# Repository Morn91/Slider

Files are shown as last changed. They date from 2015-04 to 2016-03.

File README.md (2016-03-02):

## Слайдер


#### Особенности устройства
- Вес всего 2 килограмма.
- Единственная центральная точка опоры.
- Возможность работы вертикально, перевернуто и т.д.
- Предназначение для компактных камер и гибридов (за которыми будущее).
- [Управление со смартфона по Bluetooth](https://github.com/Morn91/Slider_Android_App).
- Небольшая цена порядка $100.

#### Важно!
Проект (устройство / изделие / агрегат) еще весьма сырой, требует много доработок (особенно [приложение для Android](https://github.com/Morn91/Slider_Android_App)), однако уже вполне работает.

Имейте ввиду, я делал его как очень легкий, под очень легкую камеру (Nikon Coolpix A, весом 300 грамм). Слайдер может не поднять тяжелую БЧЗ при вертикальной работе или опрокидываться / крениться с ней при работе горизонтальной. Лучше всего использовать его с камерами вроде моей, Sony NEX, GoPro и т.д.

Мне бы не помешала помощь в развитии устройства. Если возьметесь делать его — не забывайте делиться результатами, трудностями и вносимыми изменениями.

#### [Инструкция (ru)](https://github.com/Morn91/Slider/issues/1)

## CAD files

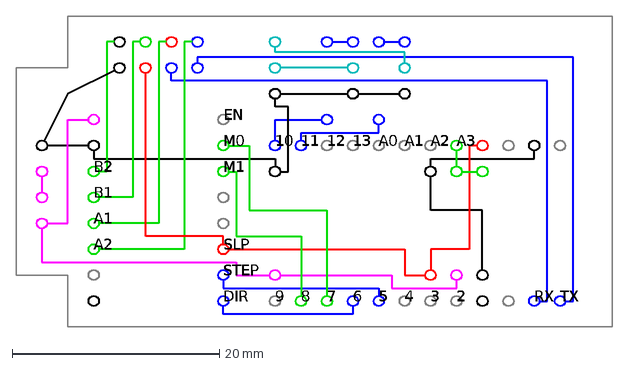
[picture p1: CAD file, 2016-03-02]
Drawings/Scheme.dxf
9
8
7
6
5
4
3
2
RX
TX
10
11
12
13
A0
A1
A2
A3
B2
B1
EN
M0
M1
SLP
STEP
DIR

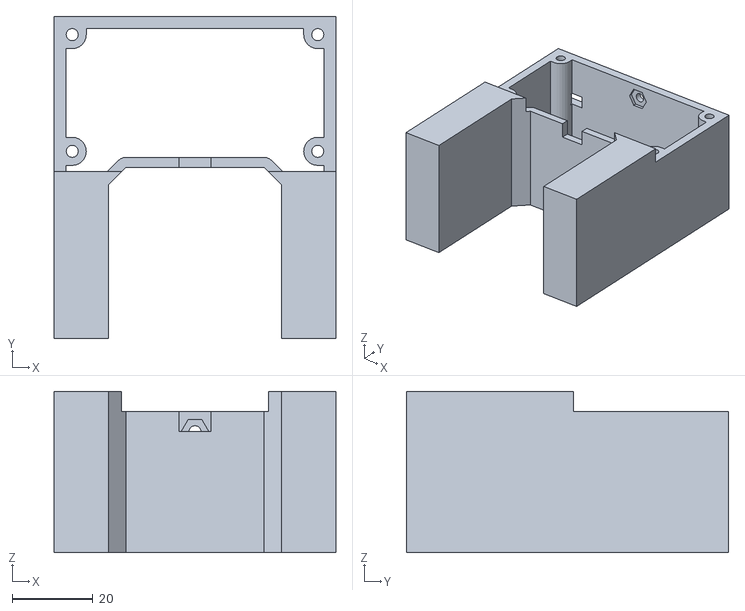
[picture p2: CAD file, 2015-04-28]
Drawings/Enclosure.stl
70.0 x 80.0 x 40.0

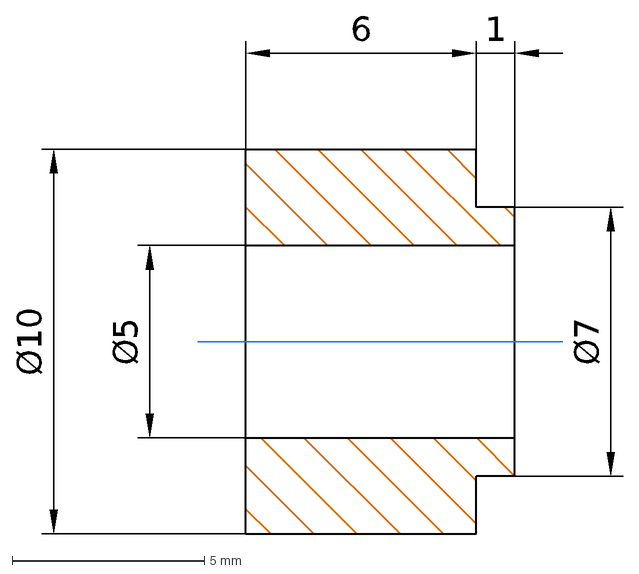
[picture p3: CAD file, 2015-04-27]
Drawings/Spacer.dxf
Ø10
Ø5
Ø7
6
1

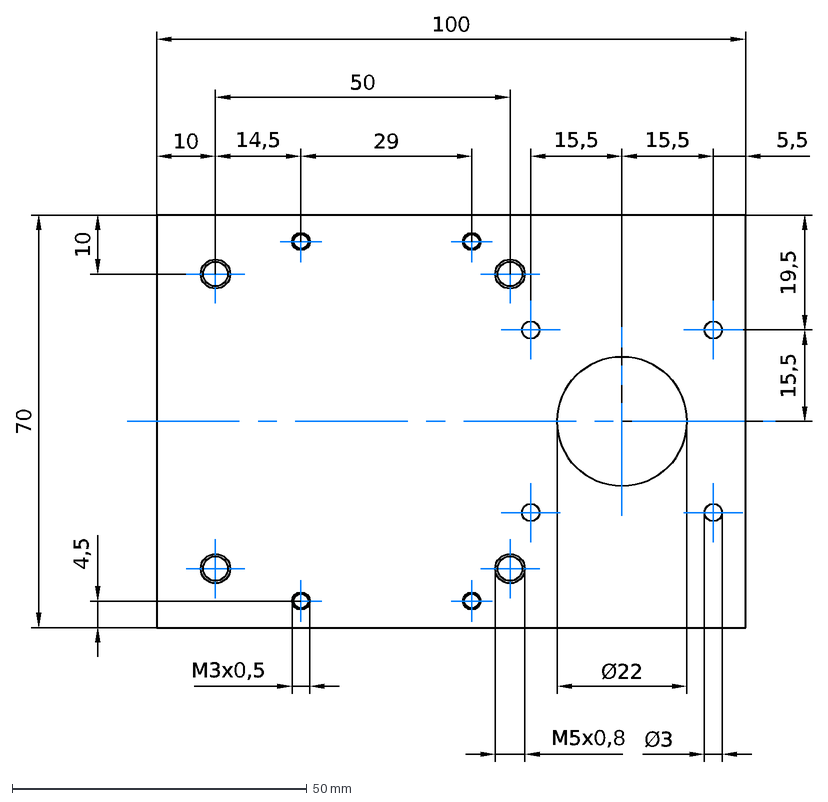
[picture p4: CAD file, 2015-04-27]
Drawings/Plate.dxf
70
14,5
100
10
М5x0,8
Ø3
15,5
5,5
19,5
Ø22
М3х0,5
29
4,5
50

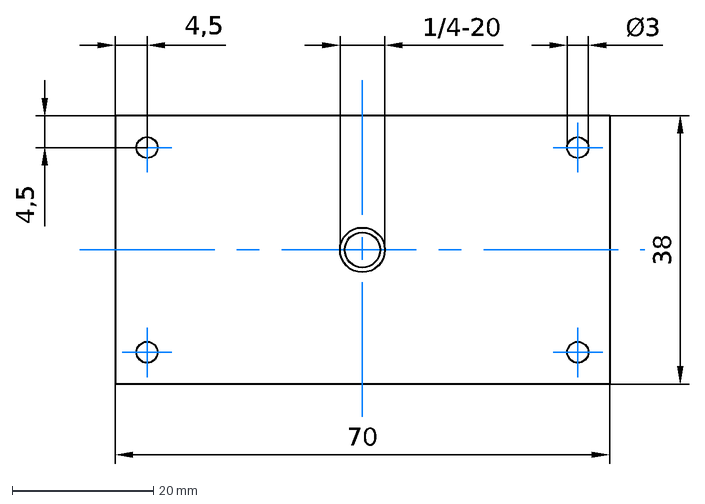
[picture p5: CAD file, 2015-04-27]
Drawings/Cover.dxf
Ø3
38
70
1/4-20
4,5

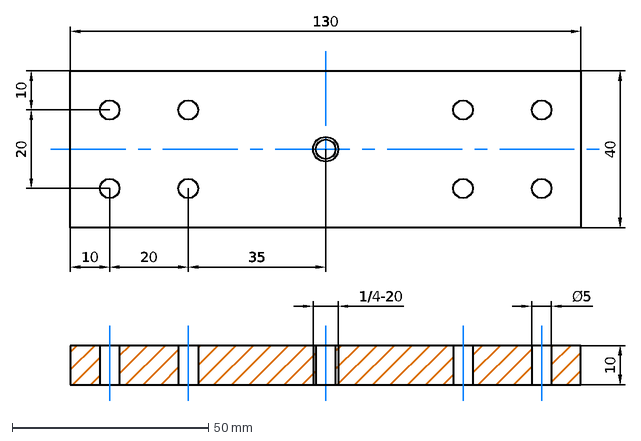
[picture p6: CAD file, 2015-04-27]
Drawings/Holder.dxf
Ø5
20
130
10
1/4-20
40
35

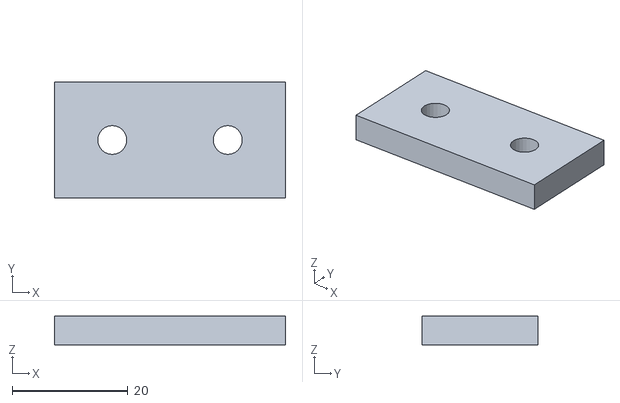
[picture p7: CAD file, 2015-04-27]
Drawings/Stopper.stl
40.0 x 20.0 x 5.00

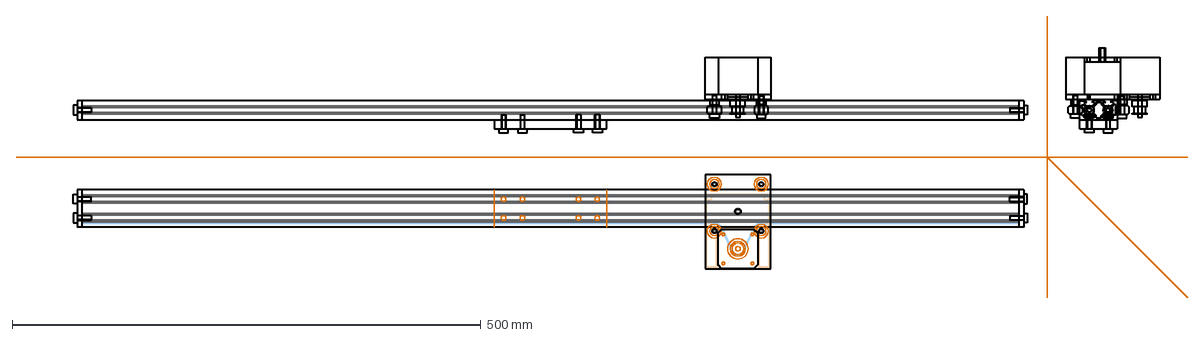
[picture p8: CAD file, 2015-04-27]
Drawings/General_view.dxf
1250.0 x 300.0 mm

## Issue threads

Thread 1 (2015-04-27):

Сборка (ru)

Morn91, 2015-04-27:
## Самодельные детали
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
#### Делаются на фрезеровочном станке:
##### Площадка ([Plate.dxf](https://github.com/Morn91/Slider/blob/master/Drawings/Plate.dxf))
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
##### Крышка ([Cover.dxf](https://github.com/Morn91/Slider/blob/master/Drawings/Cover.dxf))
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
##### Держатель ([Holder.dxf](https://github.com/Morn91/Slider/blob/master/Drawings/Holder.dxf))
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
#### Делаются на токарном станке:
##### Втулки ([Spacer.dxf](https://github.com/Morn91/Slider/blob/master/Drawings/Spacer.dxf))
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
#### Печатаются на 3D-принтере:
##### Корпус ([Enclosure.stl](https://github.com/Morn91/Slider/blob/master/Drawings/Enclosure.stl))
##### Стопоры ([Stopper.stl](https://github.com/Morn91/Slider/blob/master/Drawings/Stopper.stl))

Morn91, 2015-04-27:
## Самодельные детали
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
#### Делаются на фрезеровочном станке:
##### Площадка ([Plate.dxf](https://github.com/Morn91/Slider/blob/master/Drawings/Plate.dxf))
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
##### Крышка ([Cover.dxf](https://github.com/Morn91/Slider/blob/master/Drawings/Cover.dxf))
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
##### Держатель ([Holder.dxf](https://github.com/Morn91/Slider/blob/master/Drawings/Holder.dxf))
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
#### Делаются на токарном станке:
##### Втулки ([Spacer.dxf](https://github.com/Morn91/Slider/blob/master/Drawings/Spacer.dxf))
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
#### Печатаются на 3D-принтере:
##### Корпус ([Enclosure.stl](https://github.com/Morn91/Slider/blob/master/Drawings/Enclosure.stl))
##### Стопоры ([Stopper.stl](https://github.com/Morn91/Slider/blob/master/Drawings/Stopper.stl))

Morn91, 2015-04-27:
## Механика
- [Профиль V-Slot 20 x 40mm](http://openbuildspartstore.com/v-slot-linear-rail/).
- [Зубчатый ремень](http://openbuildspartstore.com/gt2-2mm-aluminum-timing-pulley-14-tooth/).
  - В целях экономии может быть заменен на ремень T2.5, которые можно найти на eBay. Главное условие: ширина ремня **5 мм** или меньше (ремни стандартной ширины 6 мм не подходят).
- [Шкив для зубчатого ремня](http://openbuildspartstore.com/gt2-2mm-timing-belt/).
  - Может быть заменен в соответствии с ремнем.
- **4** [колеса Mini V Wheel](http://openbuildspartstore.com/delrin-mini-v-wheel/).
- **8** [мини-подшипников](http://openbuildspartstore.com/mini-ball-bearing-5x10x4-2/).
  - По два на колесо. Это подшипники MR105 ZZ, которые можно купить на eBay дешевле.
- **4** [шайбы](http://openbuildspartstore.com/mini-v-wheel-precision-shim/).
  - Ставятся внутрь колеса, между подшипниками. Можно выточить на токарном станке.
- **10** [гаек Tee Nuts](http://openbuildspartstore.com/tee-nuts-25-pack/).
  - Служат для присоединения зубчатого ремня и держателя.
- [Шаговый мотор Nema 17 (42BYGHW609)](http://roboino.ru/product/a58)
  - Можно заменить на другой с похожими характеристиками. Главное условие — питание от **5 вольт**, иначе придется добавлять в схему повышающий преобразователь.
- Штативная головка.
  - Сам использую и рекомендую **Slik SBH-100 DQ**, но кого-то может не устроить цена.

Morn91, 2015-04-27:
## Электроника
- Контроллер Arduino Pro Mini.
- [Драйвер Pololu DRV8834](http://robototehnika.ru/e-store/catalog/203/1358/).
  - Весьма трудно найти. Заказывать поштучно с [офф-сайта](https://www.pololu.com/product/2134) не выгодно из-за цены доставки. При крайней необходимости возможно заменить на A4988 c добавлением в схему повышающего преобразователя и изменением схемы и скетча.
- Модуль Bluetooth HC-06.
  - HC-05 и другие тоже подойдут.
- Понижающий DC-DC преобразователь.
  - Максимально компактный.
- Держатель для двух 18650-аккумуляторов.

Morn91, 2015-04-27:
## Крепеж
- **2** установочных винта M3х5.
- **2** установочных винта M5х4.
- **4** винта М5х20.
- **12** винтов М5х15.
- **4** винта М3х45.
- **4** винта М3х8.
- **2** потайных винта М3х8.
- **2** гайки М3.

Morn91, 2015-04-27:
## Инструменты
- Преобразователь USB-UART.
- Метчик 1/4-20.
- Лерка 1/4-20.
- Шестигранник 1.5 мм.
- Шестигранник 2.5 мм.
- **2** прямые руки.
- Голова.

Morn91, 2015-04-27:
1

Morn91, 2015-04-27:
2

Morn91, 2015-04-27:
3

Morn91, 2015-04-27:
4

Morn91, 2015-04-27:
5

Morn91, 2015-04-27:
Запасной блок.

Morn91, 2015-04-27:
Запасной блок.

Morn91, 2015-04-27:
Запасной блок.

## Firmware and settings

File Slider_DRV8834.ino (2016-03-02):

#include <AccelStepper.h>
#include <TimerOne.h>

#define STEP 5
#define DIR 6
#define M0 7
#define M1 8
#define FOCUS 10
#define SHUTTER 11
#define BATTERY 3
#define MOTOR_MAX 750
#define DRIVER_MAX 10000
#define COEFFICIENT 1

AccelStepper stepper(AccelStepper::DRIVER, STEP, DIR);

float path, motorSpeed = 0, time = 0, elapsed = 0;
int accelType = 0, dir = 0, micRes[2] = {0, 1};
unsigned long start = 0;

void setup() {
  path = 900 / 2.5 / 16 * 200;
  //path (steps) = path (mm) / timing belt pitch (mm) / teeths on pulley * steps per turnover;
  Serial.begin(9600);
  pinMode(13, OUTPUT);
  pinMode(FOCUS, OUTPUT);
  pinMode(SHUTTER, OUTPUT);
  stepper.setMaxSpeed(DRIVER_MAX);
  stepper.setSpeed(0);
  Timer1.initialize(20);
  Timer1.attachInterrupt(runByTimer);
}

void loop() {
  if (start)
    work();
  else
    tuning();
}

void runByTimer() {
  stepper.runSpeed();
}

void tuning() {
  if(Serial.available() > 0) {
    char val = Serial.read();
    switch(val) {
    case '*':
      report();
      break;
    case '+':
      delay(100);
      char buffer[20];
      int i = 0, tmpTime = 0;
      while(Serial.available() && i < 19)
        buffer[i++] = Serial.read();
      buffer[i++] = '\0';
      sscanf(buffer, "%d %d %d", &dir, &accelType, &tmpTime);
      if((accelType == 0 && path / tmpTime <= MOTOR_MAX) || (accelType != 0 && path / tmpTime * 2 <= MOTOR_MAX)) {
        time = tmpTime;
        work();
      }
      break;
    }
  }
}

void work() {
  if(Serial.available() > 0) {
    char val = Serial.read();
    if(val == '-') {
      stop();
      return;
    }
    if(val == '*')
      report();
  }
  if(start == 0) {
    start = millis();
    digitalWrite(13, HIGH);
    digitalWrite(FOCUS, HIGH);
    digitalWrite(SHUTTER, HIGH);
  }
  elapsed = (millis() - start) / 1000.0;
  if(elapsed < time) {
    switch(accelType) {
    case 0:
      motorSpeed = path / time;
      break;
    case 1:
      motorSpeed = 2.0 * path * elapsed / time / time;
      break;
    case 2:
      motorSpeed = 2.0 * path * (time - elapsed) / time / time;
      break;
    case 3:
      if(elapsed * 2.0 < time)
        motorSpeed = 4.0 * path * elapsed / time / time;
      else
        motorSpeed = 4.0 * path * (time - elapsed) / time / time;
      break;
    case 4:
      if(elapsed * 2.0 < time)
        motorSpeed = 4.0 * path * (time / 2.0 - elapsed) / time / time;
      else
        motorSpeed = 4.0 * path * (elapsed - time / 2.0) / time / time;
      break;
    default:
      stop();
      return;
    }
    while(motorSpeed * micRes[1] * 2 <= DRIVER_MAX && micRes[1] < 32)
      micRes[1] *= 2;
    while(motorSpeed * micRes[1] > DRIVER_MAX && micRes[1] > 1)
      micRes[1] *= 0.5;
    if(micRes[0] != micRes[1])
      microstep();
    if(dir)
      stepper.setSpeed(-motorSpeed * micRes[1]);
    else
      stepper.setSpeed(motorSpeed * micRes[1]);
  }
  else
    stop();
}

void microstep() {
  switch(micRes[1]) {
  case 1:
    pinMode(M0, OUTPUT);
    digitalWrite(M0, LOW);
    digitalWrite(M1, LOW);
    break;
  case 2:
    pinMode(M0, OUTPUT);
    digitalWrite(M0, HIGH);
    digitalWrite(M1, LOW);
    break;
  case 4:
    pinMode(M0, INPUT);
    digitalWrite(M1, LOW);
    break;
  case 8:
    pinMode(M0, OUTPUT);
    digitalWrite(M0, LOW);
    digitalWrite(M1, HIGH);
    break;
  case 16:
    pinMode(M0, OUTPUT);
    digitalWrite(M0, HIGH);
    digitalWrite(M1, HIGH);
    break;
  case 32:
    pinMode(M0, INPUT);
    digitalWrite(M1, HIGH);
    break;
  }
  micRes[0] = micRes[1];
}

void stop() {
  digitalWrite(13, LOW);
  digitalWrite(FOCUS, LOW);
  digitalWrite(SHUTTER, LOW);
  stepper.setSpeed(0);
  start = 0;
  time = 0;
  elapsed = 0;
  while(Serial.available() > 0)
    Serial.read();
}

void report() {
  int i, voltage = 0;
  for(i = 0; i < 20; i++) {
    voltage += analogRead(BATTERY);
    delay(5);
  }
  Serial.print(dir);
  Serial.print('\t');
  Serial.print(accelType);
  Serial.print('\t');
  Serial.print(time, 0);
  Serial.print('\t');
  Serial.print(time - elapsed, 0);
  Serial.print('\t');
  Serial.print(voltage * COEFFICIENT / i, 0);
  Serial.print('\n');
}

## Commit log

2015-04-27 Create General view.dxf
    [General view.dxf]
2015-04-27 Create Список деталей (ru).csv
    [Список деталей (ru).csv]
2015-04-27 Update Список деталей (ru).csv
    [Список деталей (ru).csv]
2015-04-27 Rename Список деталей (ru).csv to Список деталей и инструментов (ru).csv
    [Список деталей и инструментов (ru).csv]
2015-04-27 Update Список деталей и инструментов (ru).csv
    [Список деталей и инструментов (ru).csv]
2015-04-27 Rename Список деталей и инструментов (ru).csv to Детали и инструменты (ru).csv
    [Детали и инструменты (ru).csv]
2015-04-27 Update Детали и инструменты (ru).csv
    [Детали и инструменты (ru).csv]
2015-04-27 Rename General view.dxf to General_view.dxf
    [General_view.dxf]
